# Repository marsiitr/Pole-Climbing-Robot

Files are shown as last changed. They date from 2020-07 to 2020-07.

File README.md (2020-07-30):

# Pole-Climbing-Robot
Srishti 2020

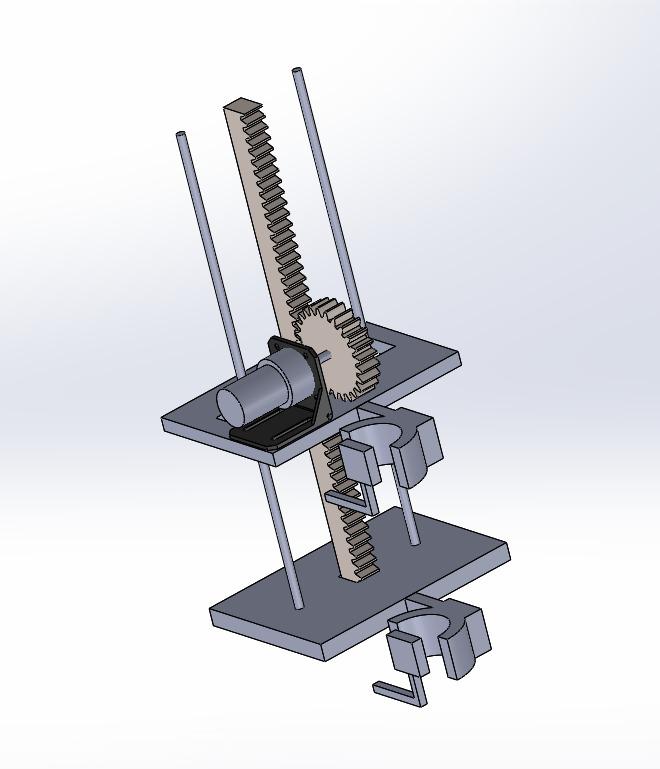
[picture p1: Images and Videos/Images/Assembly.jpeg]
Final Product

## Abstract
<p align="justify">Pole climbing robot utilizes a rack and pinion system to perform vertical motion up and down a pole, with the caterpillar motion of the top plate and bottom plate. The robot can climb up the poles within a certain range of diameters.</p>

## Motivation
<p align="justify">Electricians and workmen have to climbup an electric pole in case of a malfunction, this leads to several accidents. This can be avoided if a robot can be made to climb the pole and perform specialised functions. As a first step towards that, this robot has been designed to climb a pole. It can also be used for surveillance and fruit harvesting.</p>

## Workflow
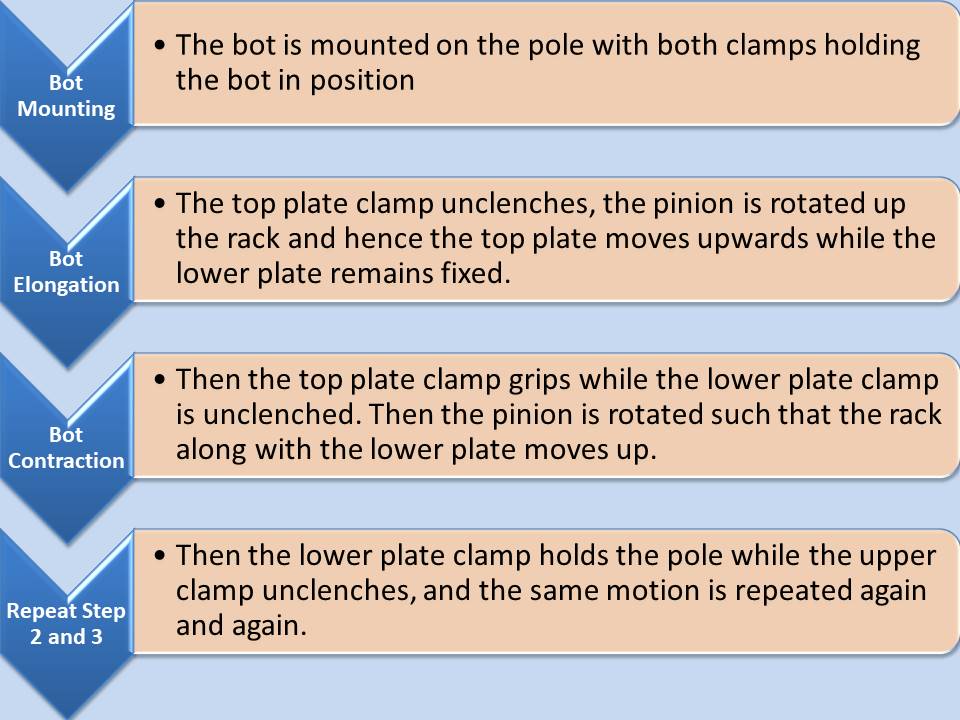
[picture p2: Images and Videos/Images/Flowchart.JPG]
Workflow


## Mechanical Aspect of the Design
1. The robot consists of a top plate and a bottom plate, both connected to clamps on thier side to hold on to the pole.
2. The clamp is 3d printed and is specifically designed for this purpose. It is padded with a soft gripping rubbery material. It's grip is loosened or tightened using the motion of a lead screw, which is fitted inside the 3d printed clamp jaw and connected below the plates with a circular ball bearing.
3. The two plate system is stabilised by two rods which pass through the top plate through linear bearings and are connected to the bottom plate.
4. The top plate is connected to the pinion and has linear bearings and a slot for accomodating the rods and the rack respectively, while the bottom plate is connected to the rack and the rods.

## Electronics Aspect of the Design
1. The micro-controller used is Arduino UNO and Cytron motor drivers.
2. The pinion is rotated by a DC motor with an encoder.
3. The lead screw of the clamp is rotated by a DC motor with an encoder.
4.  12 V battery is used for powering the system

## Cost Structure 
| Sr. No. | Product | Cost(In Rupees) | Quantity | Subtotal| 
|---|---|---|---|----|
| 1. | Arduino UNO | 500 | 1 | 500 |
| 2. | Encoder | 1500 | 3 | 4500 |
| 3. | DC motor | 300 | 2 | 600 |
| 4. | Cytron MDD | 1700 | 2 | 3400 |
| 5. | Lead screw | 450 | 1 | 450 |
| 6. | Brass Rod | 80 | 1 | 80 |
| 7. | Linear Bearing | 170 | 2	| 340 |
| 8. | Circular Bearing | 40 | 2 | 80 |
| 9. | 12 V battery | 1500 | 1 | 1500 |
| 10. | Miscellaneous | 300 | - | 300 |
|  | **Total** | | | 11,750 |

## Applications
 1. Fruit harvesting
 2. Painting poles
 3. Cleaning lamp post
 4. Accessing wind turbines or street light for inspection
 5. Surveillance
 6. Fix Telecom cables

## Limitations
 1. The lead screw mechanism is slower than we'd desire.
 2. The rack and pinion is slightly slower than the faster actuators like hydraulic and pneumatic.
 3. The clamp design limits the width of the rod that can be climbed.
 4. The bot's weight increases because of the several actuators and other parts.

## Future Improvement
 1. Design a prototype at big size, which can be used for pole with different diameters and high payloads capability
 2. Replace the grippers with a better gripping mechanism ( Ex: Soft robot gripper or more number of grippers to climb poles of any texture and diameter)
 3. Remotely control the robot from a smart device.

## Team members
 1. [Akshara Singh](https://github.com/ItsAshChase)
 2. [Nitika Gupta](https://github.com/Nitikagupta16)
 3. [Parag Garg](https://github.com/paraggarg1102)
 4. [Sarthak Sharma](https://github.com/DanielLarusso1)

## Mentors
 1. [Aditya Raj]()
 2. [Rishika Chandra](https://github.com/chandrarishika14)

## References
 1. [Rack and Pinion mechanism]( https://www.britannica.com/technology/rack-and-pinion)
 2. [Lead screw clamps](https://in.misumi-ec.com/vona2/mech)
 3. [Pole Climbing basics]( http://engineering.nyu.edu/mechatronics/projects/ME7836/spring2017/Arduino/4mini1/report.pdf)

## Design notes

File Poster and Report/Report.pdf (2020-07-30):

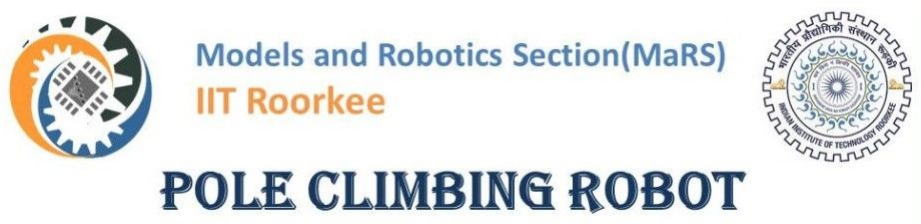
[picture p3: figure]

# PROJECT REPORT

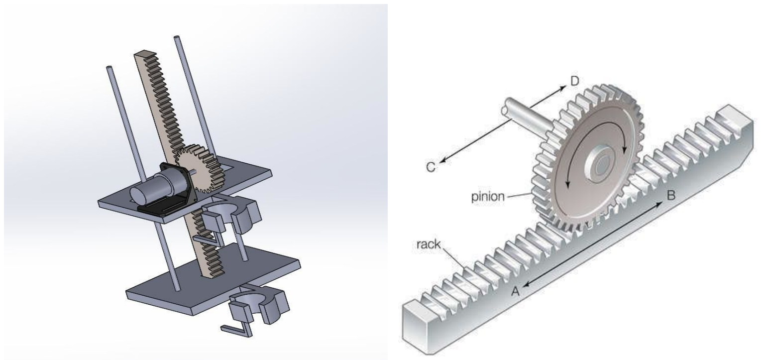
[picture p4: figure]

### A. Abstract

Pole climbing robot utilizes a rack and pinion system to perform vertical motion up and down a pole, with the caterpillar motion of the top plate and bottom plate. The robot can climb up the poles within a certain range of diameters. The robot is mounted on the pole, then the top plate clamp unclenches, the pinion is rotated up the rack and hence the top plate moves upwards while the lower plate remains fixed. Then the top plate clamp grips while the lower plate clamp is unclenched. Then the pinion is rotated such that the rack along with the lower plate moves up. Then the lower plate clamp holds the pole while the upper clamp unclenches, and the same motion is rotated again and again.

### B. Motivation

Electricians and workmen have to climb up an electric pole in case of a malfunction, this leads to several accidents. This can be avoided if a robot can be made to climb the pole and perform specialised functions. As a first step towards that, this robot has been designed to climb a pole. It can also be used for surveillance and fruit harvesting.

### C. Mechanical Aspect of the Design

The robot consists of a top plate connected to the pinion and a clamp whereas the bottom plate is connected to the rack and the lower clamp. The clamp is 3d printed and is specifically designed for this purpose. It is padded with a soft gripping rubbery material. It's grip is loosened or tightened using the motion of a lead screw. The two plate system is stabilised by two rods which pass through the top plate through linear bearings and are connected to the bottom plate.

### D. Electronics Aspect of the Design

The microcontroller used is Arduino UNO and Cytron motor drivers. The pinion is rotated by a DC motor with an encoder. The lead screw of the clamp is rotated by a DC motor with an encoder.

### E. Cost Structure (In Rupees)

Sr. No. | Equipment | Cost | Quantity | Subtotal
1. | Arduino UNO | 500 | 1 | 500
2. | Encoder | 1500 | 3 | 4500
3. | DC Motor | 300 | 3 | 900
4. | Cytron MDD | 1700 | 2 | 3400
5. | Lead Screw | 450 | 1 | 450
6. | Brass Rod | 80 | 1 | 80
7. | Linear Bearing | 170 | 2 | 340
8. | Circular Bearing | 40 | 2 | 80
9. | 12 V Battery | 1500 | 1 | 1500
10. | Miscellaneous | 300 | - | 300
| Total | | | 12,050

### F. Workflow

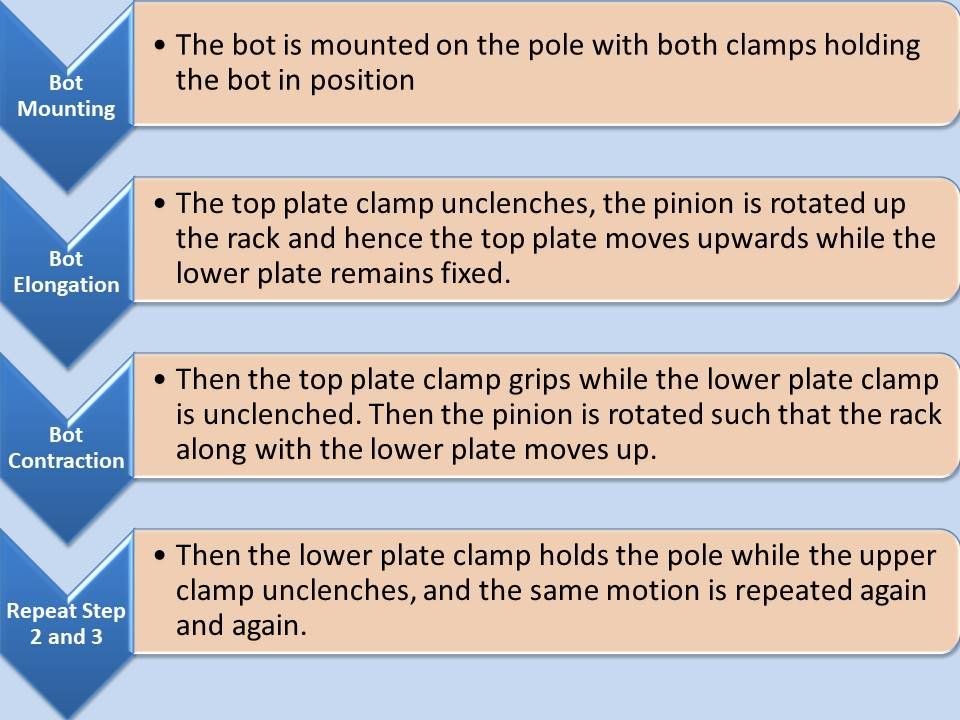
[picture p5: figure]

### G. Applications

1. Fruit harvesting: This bot can be used to climb us trees with slender stems, and can be mounted with a cutting device
2. Painting poles: With proper painting equipment, it could be used to paint poles
3. Cleaning lamp post: Several lamp posts become inefficient, after they become unclean and dusty,these robots can help clean them.
4. Accessing wind turbines or street light for inspection: Wind turbines are expensive and delicate, they can inspected using this bot, after mounting this robot with a camera
5. Surveillance: This robot can be used by defense services to climb up trees or poles to spy on enemy camps or for surveillance of our own camps.
6. Fix Telecom cables: Many accidents happen, while fixing telecom cables, they can be avoided by loading the requisite equipment on the robot.

### H. Limitations

1. The lead screw mechanism is slower than we'd desire.
2. The rack and pinion is slightly slower than the faster actuators like hydraulic and pneumatic.
3. The clamp design limits the width of the rod that can be climbed.
4. The bot's weight increases because of the several actuators and other parts.

### I. Future Improvement

1. Design a prototype at big size, which can be used for pole with different diameters and high payloads capability
2. Replace the grippers with a better gripping mechanism ( Ex: Soft robot gripper or more number of grippers to climb poles of any texture and diameter)
3. Remotely control the robot from a smart device.

### J. Team members

1. Akshara Singh
2. Nitika Gupta
3. Parag Garg
4. Sarthak Sharma

### K. Mentors

1. Aditya Raj
2. Rishika Chandra

### L. Proper References with link

1. Rack and Pinion mechanism: https://www.britannica.com/technology/rack-and-pinion

2. Lead screw clamps: https://in.misumi-ec.com/vona2/mech
3. Pole Climbing basics:
http://engineering.nyu.edu/mechatronics/projects/ME7836/spring2017/Arduino/4mini1/report.pdf

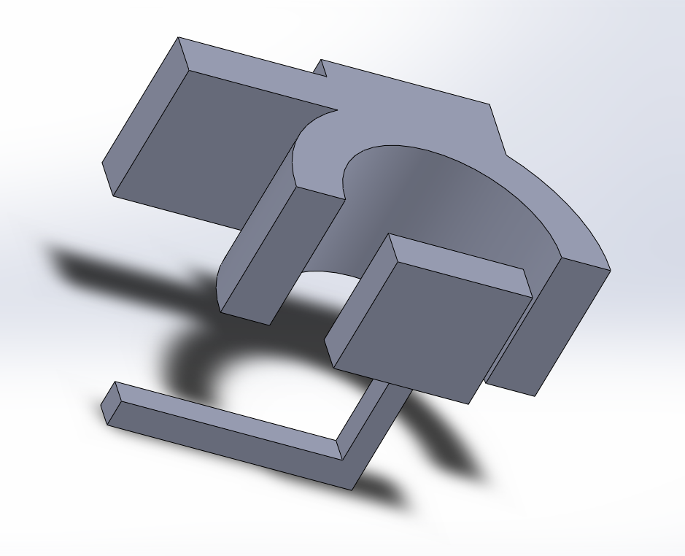
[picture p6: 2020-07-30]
Mechanical design/clamp/Clamp.PNG

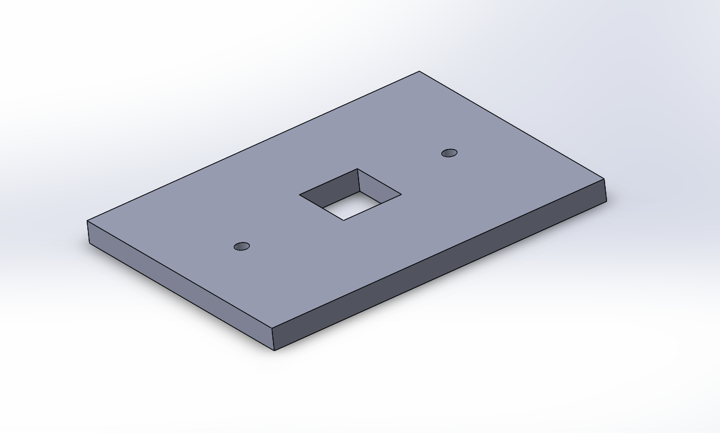
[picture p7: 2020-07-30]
Mechanical design/top plate/TopPlate.PNG

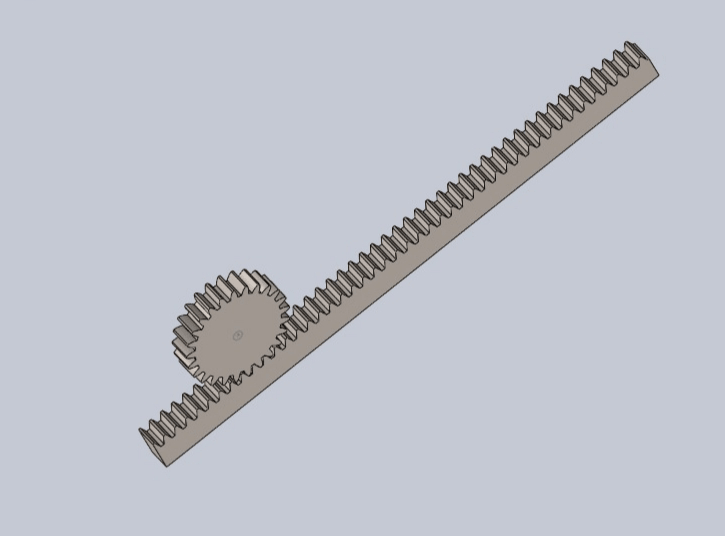
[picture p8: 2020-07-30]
Mechanical design/rack and pinion/rack and pinion.png

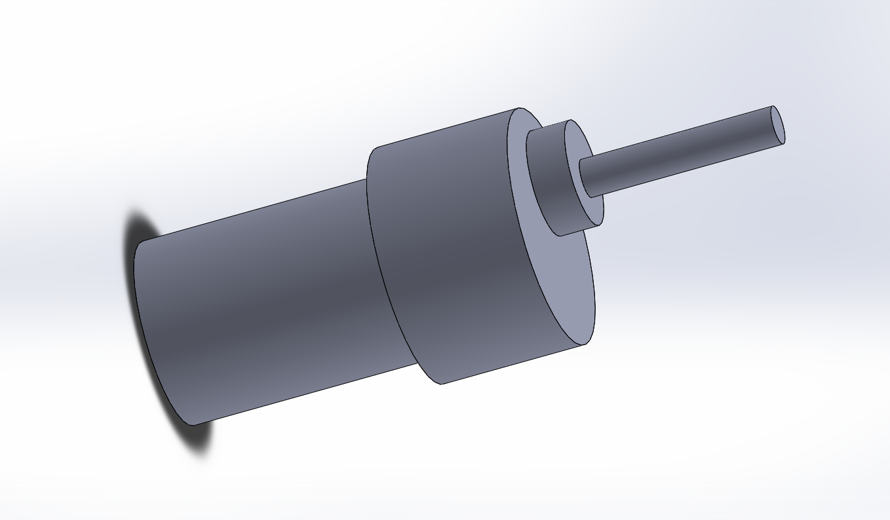
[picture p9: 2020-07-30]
Mechanical design/motor/Motor.PNG

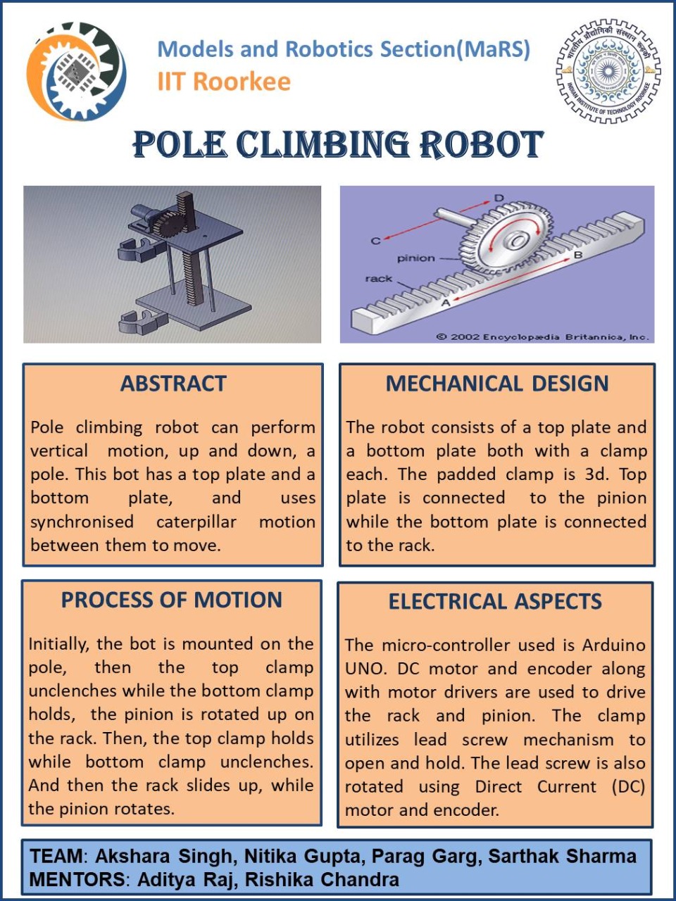
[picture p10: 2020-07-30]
Poster and Report/Poster.jpg

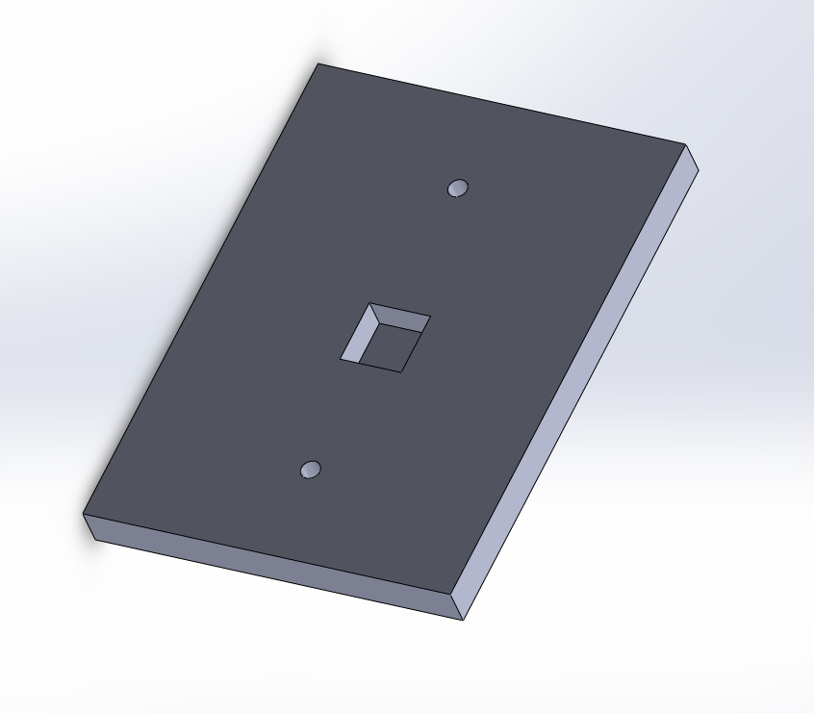
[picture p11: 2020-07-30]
Mechanical design/base plate/Base.PNG

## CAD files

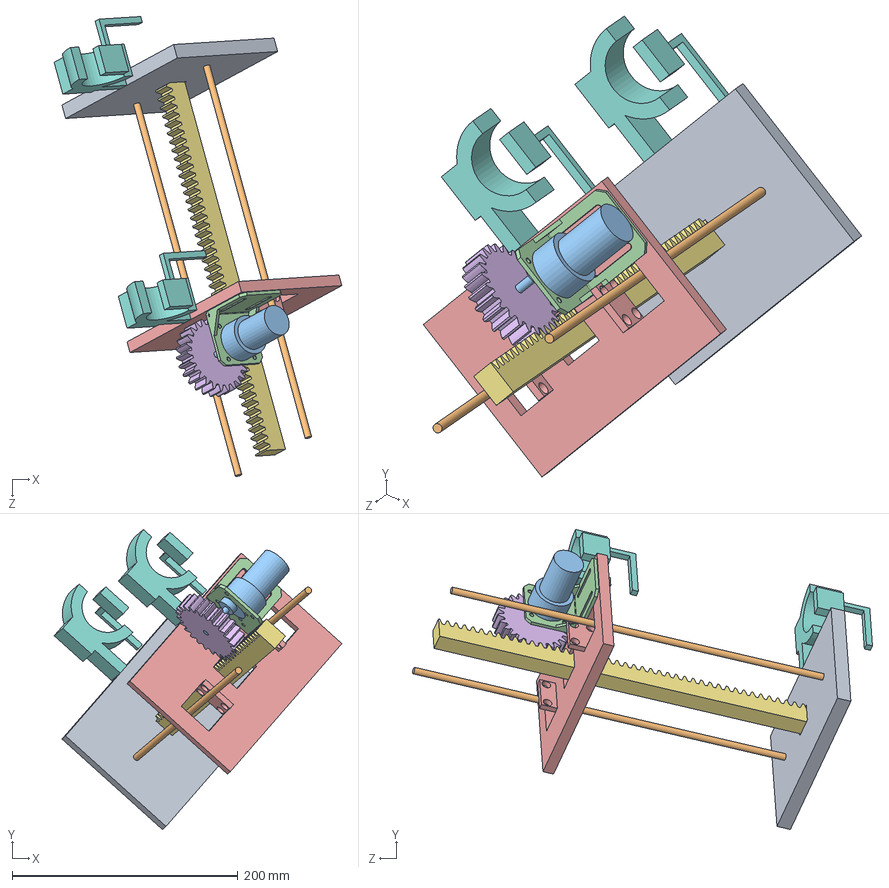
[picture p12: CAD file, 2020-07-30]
Mechanical design/Complete CAD.SLDASM
255.1 x 266.0 x 407.9 mm
plate
rod x 2
motor
MotorMount_NEMA
TopPlate (1)
spur gear_ai
rack spur rectangular_ai
Final Clamp (4) x 2

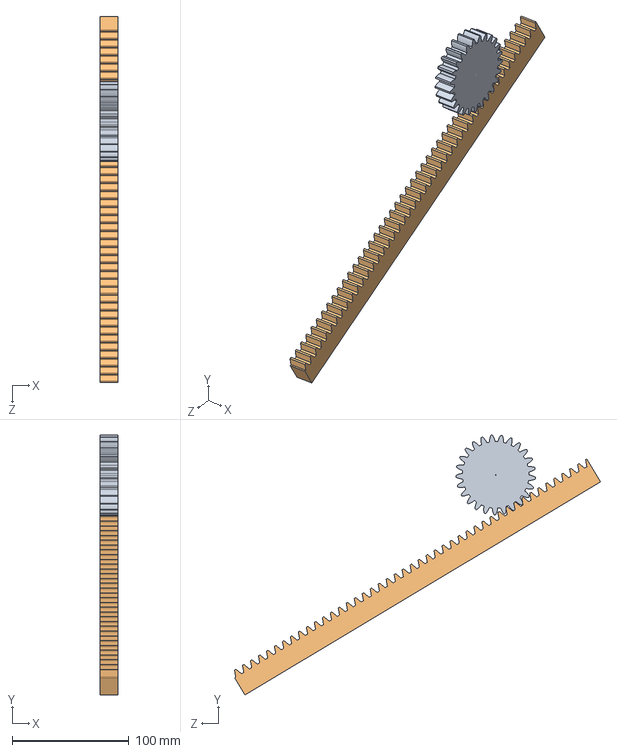
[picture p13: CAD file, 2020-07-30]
Mechanical design/rack and pinion/Assem3 (1).SLDASM
15.2 x 223.0 x 314.0 mm
spur gear_ai
rack spur rectangular_ai

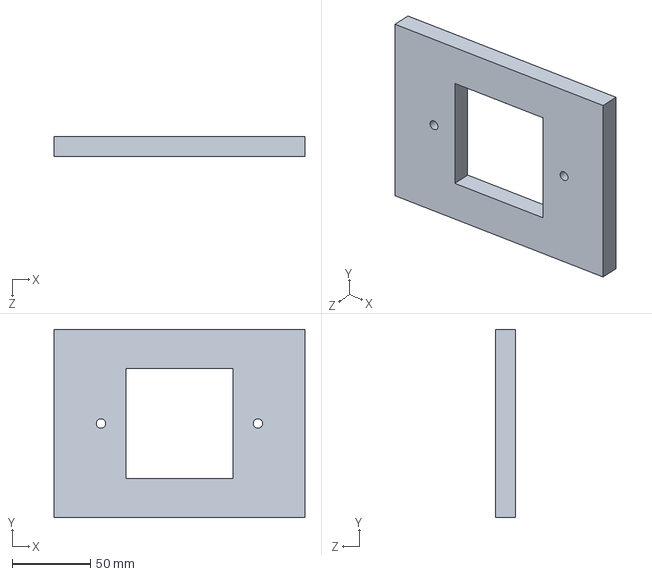
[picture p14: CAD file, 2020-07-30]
Mechanical design/base plate/plate.SLDPRT
160.0 x 120.0 x 12.7 mm

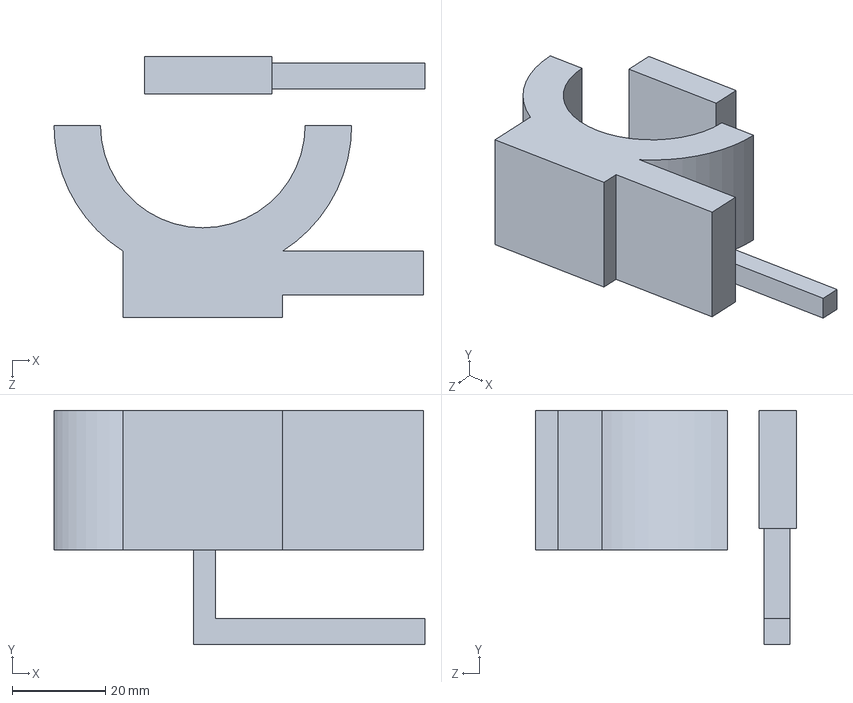
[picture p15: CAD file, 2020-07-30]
Mechanical design/clamp/Final Clamp (4).SLDPRT
79.8 x 50.4 x 56.1 mm

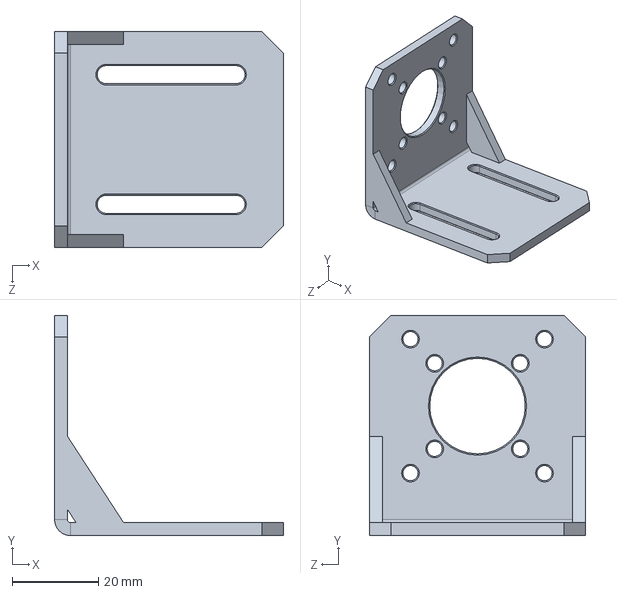
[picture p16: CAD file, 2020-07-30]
Mechanical design/motor mount/MotorMount_NEMA.SLDPRT
53.0 x 51.0 x 50.0 mm

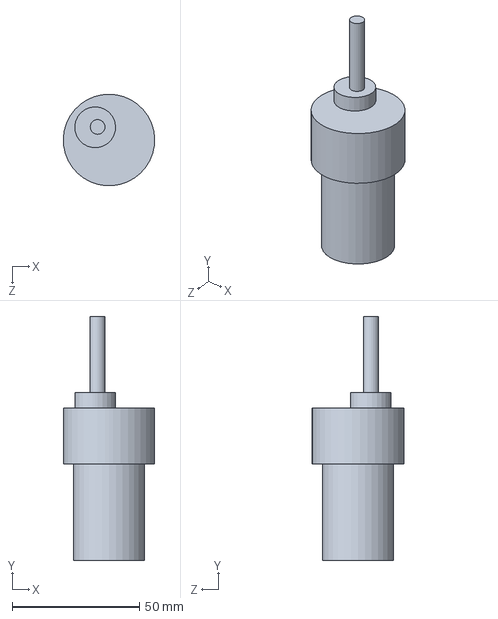
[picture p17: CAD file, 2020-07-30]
Mechanical design/motor/motor.SLDPRT
36.0 x 96.0 x 36.0 mm

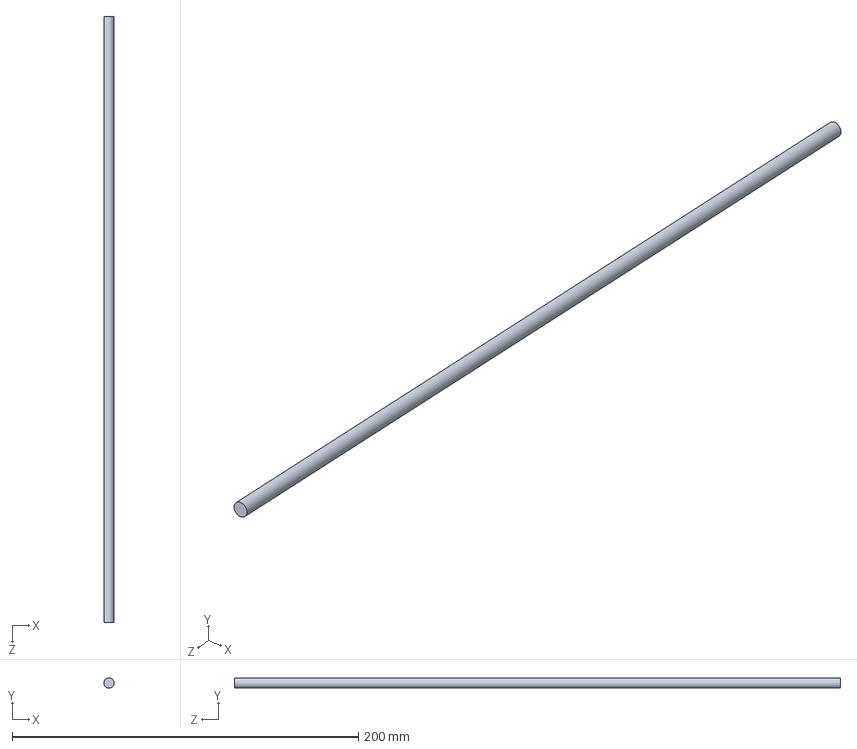
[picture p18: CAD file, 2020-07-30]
Mechanical design/rod/rod.SLDPRT
6.00 x 6.00 x 350.0 mm

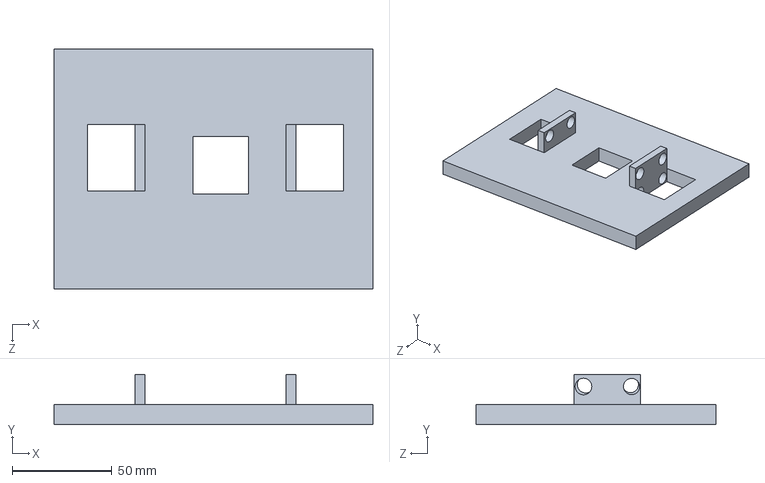
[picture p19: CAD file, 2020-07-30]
Mechanical design/top plate/TopPlate (1).SLDPRT
159.8 x 25.1 x 120.0 mm

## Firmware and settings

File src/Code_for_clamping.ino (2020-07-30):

int dir1 =7;
int pwm1 = 9;
int velocity1=0;
int dir2 =8;
int pwm2 = 10;
int velocity2=0;
int pinA=2;
int pinB=3;
int counter=0;
int aState;
int d;
int enco1;

//int LastState;




void setup() {
  pinMode (dir1, OUTPUT);
  pinMode (dir2, OUTPUT);
  pinMode (pinA,INPUT);
  pinMode (pinB,INPUT);
  attachInterrupt(0, encoder1, CHANGE);
  Serial.begin(9600);
  aState =  digitalRead(pinA);
  enco1 = 0.3*counter;
  d = 0.2*enco1/360;

}

void loop() {
  velocity1= velocity1 + 110;
  if(d < 6 && d > 1.5)
  {
  digitalWrite( dir1, HIGH);
  analogWrite( pwm1, velocity1);
  delay(1000);
  }
  else
  {
  digitalWrite( dir1, LOW);
  analogWrite( pwm1, velocity1);
  delay(1000);
  }
  velocity2 = velocity2 + 110;
  if(d < 6 && d > 1.5)
  {
  digitalWrite( dir2, LOW);
  analogWrite( pwm2, velocity2);
  delay(1000);
  }
  else
  {
  digitalWrite( dir2, HIGH);
  analogWrite( pwm2, velocity2);
  delay(1000);
  }
 if(aState!= counter)
  {
  aState== counter;
  Serial.println(counter);
  }
}
void encoder1()
{
  if(digitalRead(pinA)== digitalRead(pinB))
  {
    counter++;
  }
  else
  {
    counter--;
  }
}

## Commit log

2020-07-28 added code for encoder and clamping by DC motor
2020-07-28 added Src for clamping
2020-07-29 Mechanical design added
    [Assem3(1).SLDASM, Complete CAD.SLDASM, Final Clamp (4).SLDPRT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]
2020-07-29 Changes done
    [Assem3(1).SLDASM, Final Clamp (4).SLDPRT, MotorMount_NEMA.SLDPRT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]
2020-07-30 Revert "added Src for clamping"
    This reverts commit d73eedf6e480c3af72885ef29c728fb277e82d86.
2020-07-30 Revert "added code for encoder and clamping by DC motor"
    This reverts commit 28d1abf02af081cfabafc2094ca00eba0531c8da.
2020-07-30 Mechanical design
    [Assem3 (1).SLDASM, Assem3(1).SLDASM, Complete CAD.SLDASM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]
2020-07-30 clamping code
